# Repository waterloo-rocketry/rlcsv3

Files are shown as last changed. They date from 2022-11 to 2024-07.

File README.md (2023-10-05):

# Remote Launch Control System

RLCS stands for Remote Launch Control System. It's purpose is to fill our rocket with ethanol and nitrous oxide, then ignite the ignition puck inside the rocket, all from a distance of 3000' away at launch control. To do so, it has control over multiple valves at the rocket, a linear actuator to disconnect the fill arm from the rocket, and 2 ignition coils inside the ignition puck.

### Repository Layout

All Arduino firmware code is in `/src`

All electrical schematics and PCB layouts are in `/schematics`

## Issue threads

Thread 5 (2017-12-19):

Finish writing the client code

akmorrison, 2017-12-19:
The client code doesn't currently work. This should be fixed.

Closed 2018-06-08.

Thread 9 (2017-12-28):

Fuses for relay boards in series with battery ground, not with battery v+

akmorrison, 2017-12-28:
The relay boards (and, to follow convention, the power boards) have inline fuses with the battery inputs, but the fuses are on the low side. Because the entire box has a common ground (and most of the battery inputs come from the same few batteries), there are multiple return paths to ground, so overdrawing current will blow multiple fuses, instead of just one (which would be ideal).

This is relatively easy to fix by moving the fuses to inline with the positive side of the battery input, but that would require having new boards made, and would mean scrapping the ones we have, and the expensive-ish hardware that is soldered to them.

This isn't a safety issue, since all batteries are still fused, but it's pretty dumb to have current return paths through multiple parallel fuses. This should be fixed, but it's not a priority to be fixed this term/competition cycle.

Closed 2020-10-31.

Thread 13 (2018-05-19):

NIO: valves on board the rocket are controlled by 4 digital outputs, not 2

amihaila, 2018-05-19:
`nio_init(...)` (and any related internal stuff) needs to be fixed to reflect this.

Closed 2018-06-08.

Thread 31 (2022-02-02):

Incorrect silkscreen labelling on the I2C relay board v3

ZTeper, 2022-02-02:
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

The silkscreen labels on the daisy chain connectors are incorrect!
Also, the pin order on the two connectors are inconsistent, which makes the rlcs wiring quite unpleasant, due to the 180-degree twist required between boards. The two connectors should have the same orientation, i.e. 12V , 5V in front, SDA, SCL in back.

Closed 2022-11-04.

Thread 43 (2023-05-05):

CAN Support Board Issues

BluCodeGH, 2023-05-05:
- Hole pattern is not correct, the board is currently too wide
- Relay should be powered from the 5-pin connector's +12V, not the actuator +12V

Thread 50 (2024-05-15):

Clientside board issue

JasonBrave, 2024-05-15:
1. Mounting holes cannot fit M3 screws
2. One of the mounting hole get in the way of arduino usb type b cable
3. One of the switch have arduino pin conflict with usb uart
4. for the board to function currently, pullup resistor on the arduino have to be desoldered

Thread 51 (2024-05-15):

Towerside power board issue

JasonBrave, 2024-05-15:
UART for ethernet adapter is on UART0, which is conflict to the USB UART onboard arduino

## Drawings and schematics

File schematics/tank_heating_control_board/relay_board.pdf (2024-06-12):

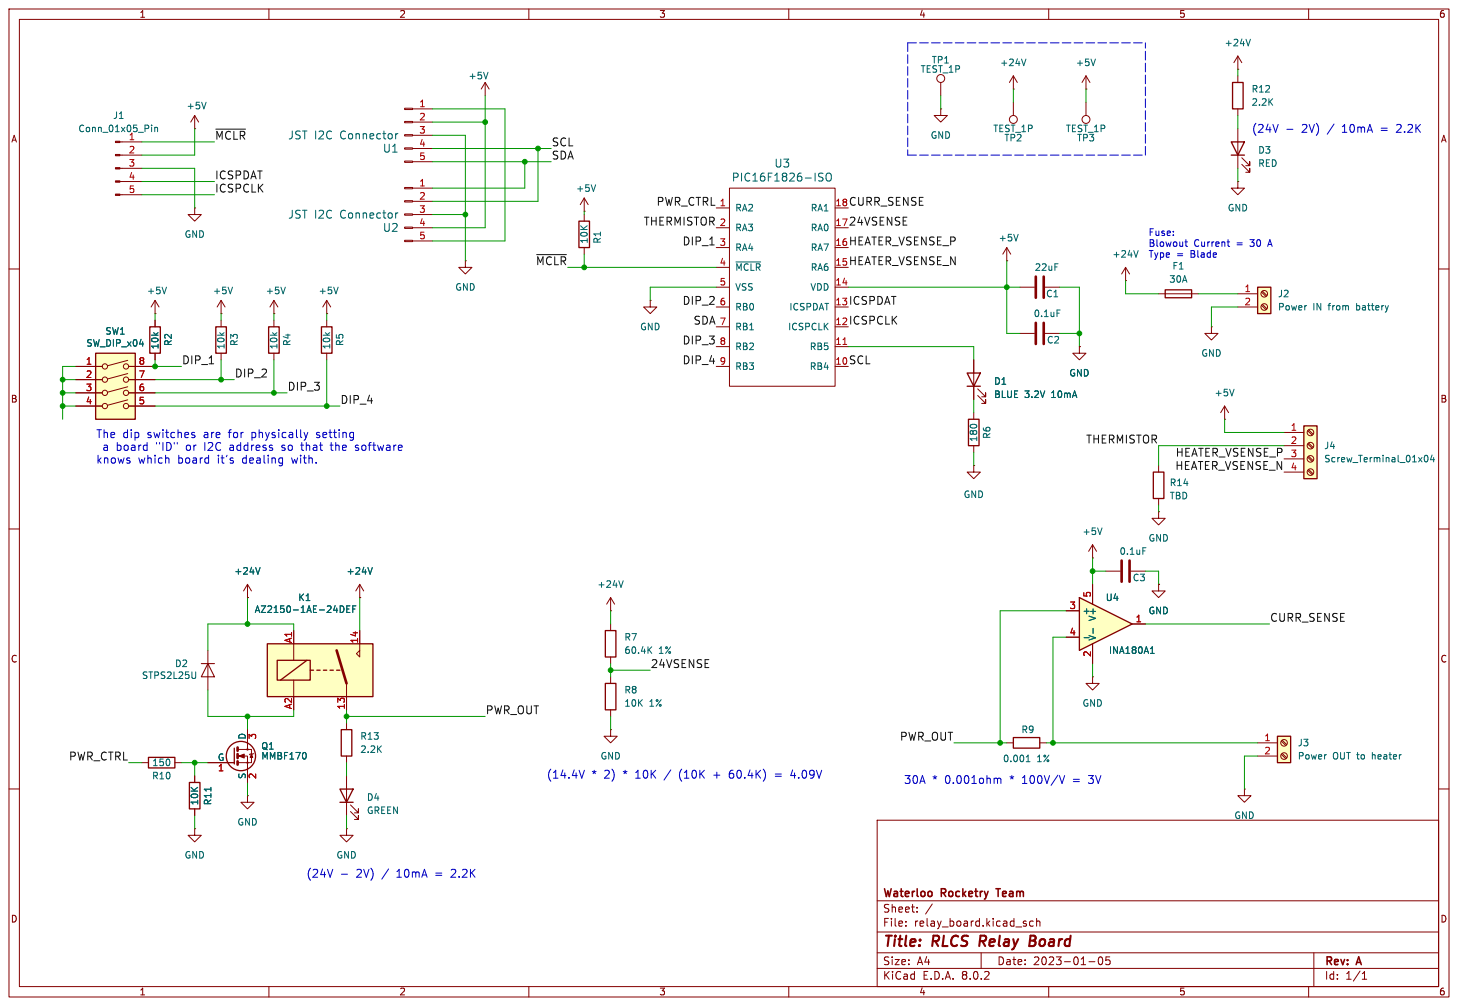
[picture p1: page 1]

a board "ID" or I2C address so that the software

Id: 1/1 Title: RLCS Relay Board

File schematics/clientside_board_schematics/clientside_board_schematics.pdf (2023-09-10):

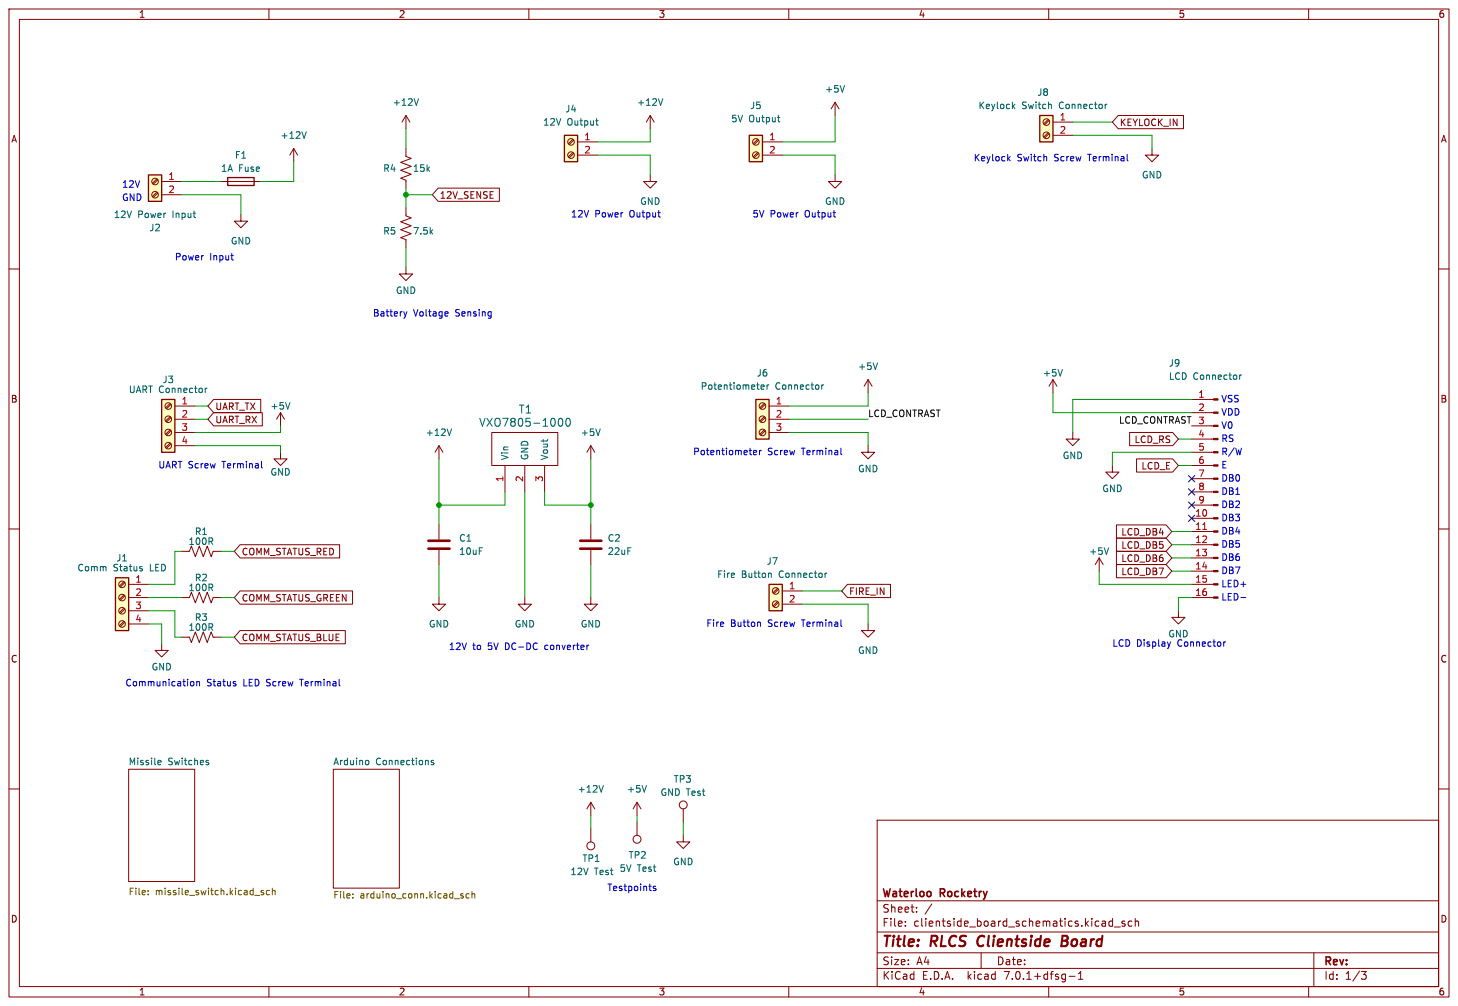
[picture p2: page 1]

Id: 1/3 Title: RLCS Clientside Board

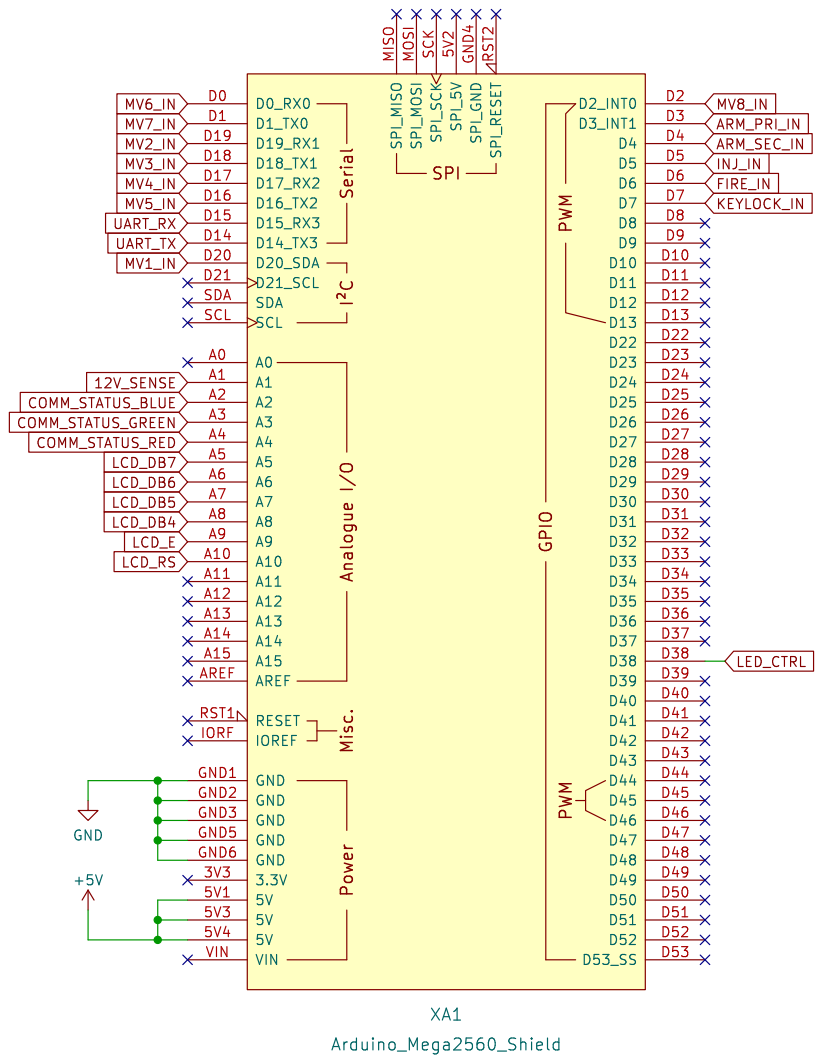
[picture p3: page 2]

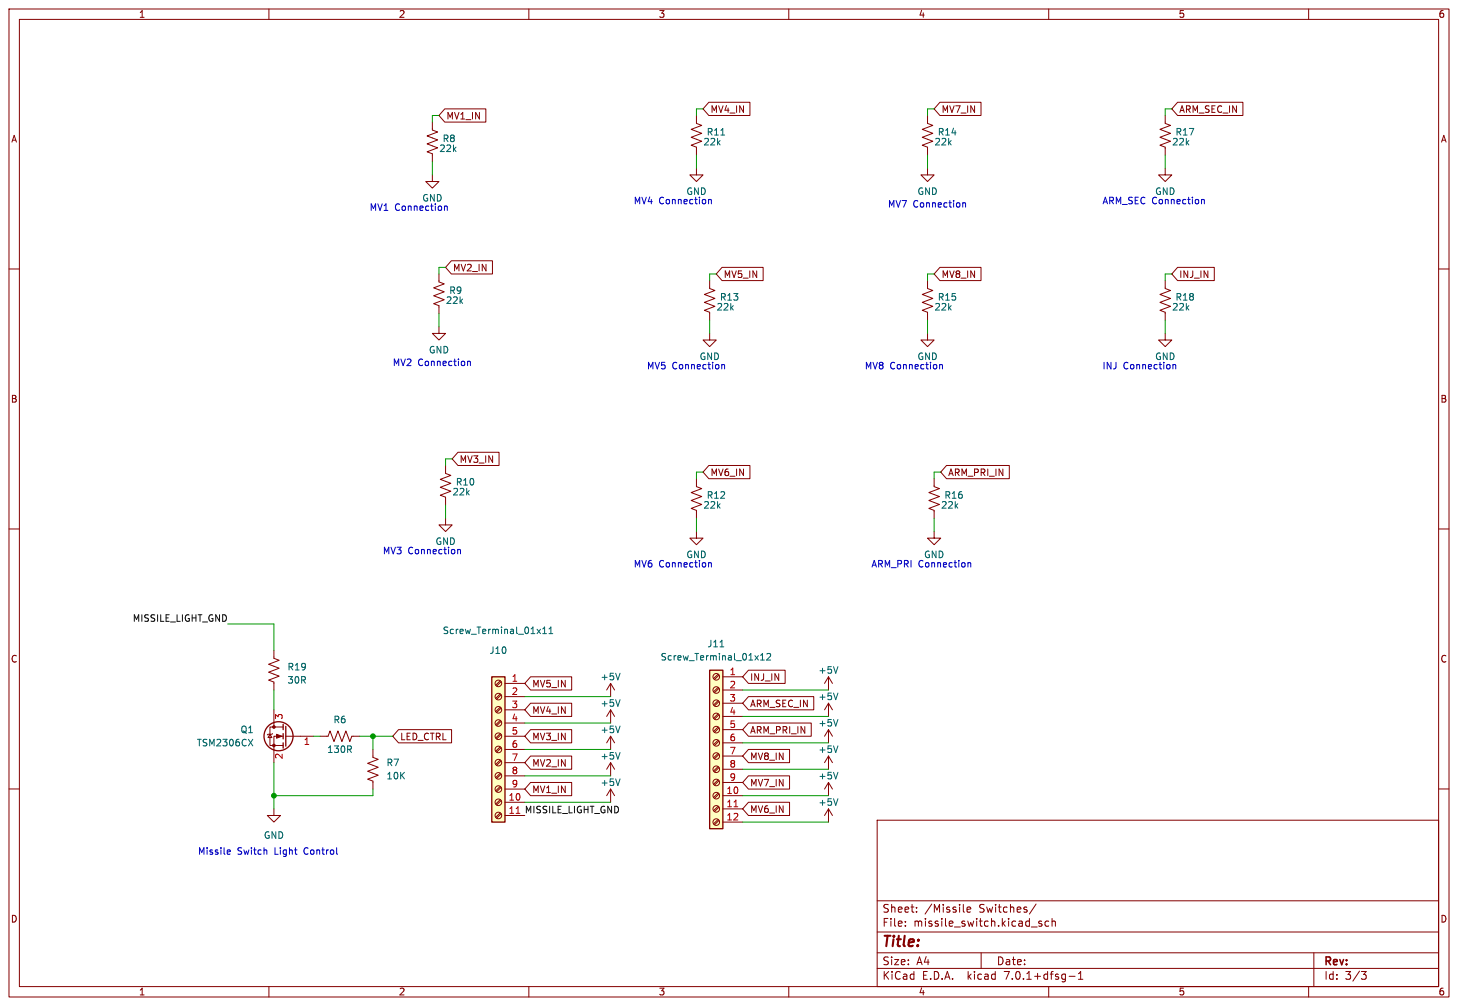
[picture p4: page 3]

INJ Connection MV4 Connection Missile Switch Light Control

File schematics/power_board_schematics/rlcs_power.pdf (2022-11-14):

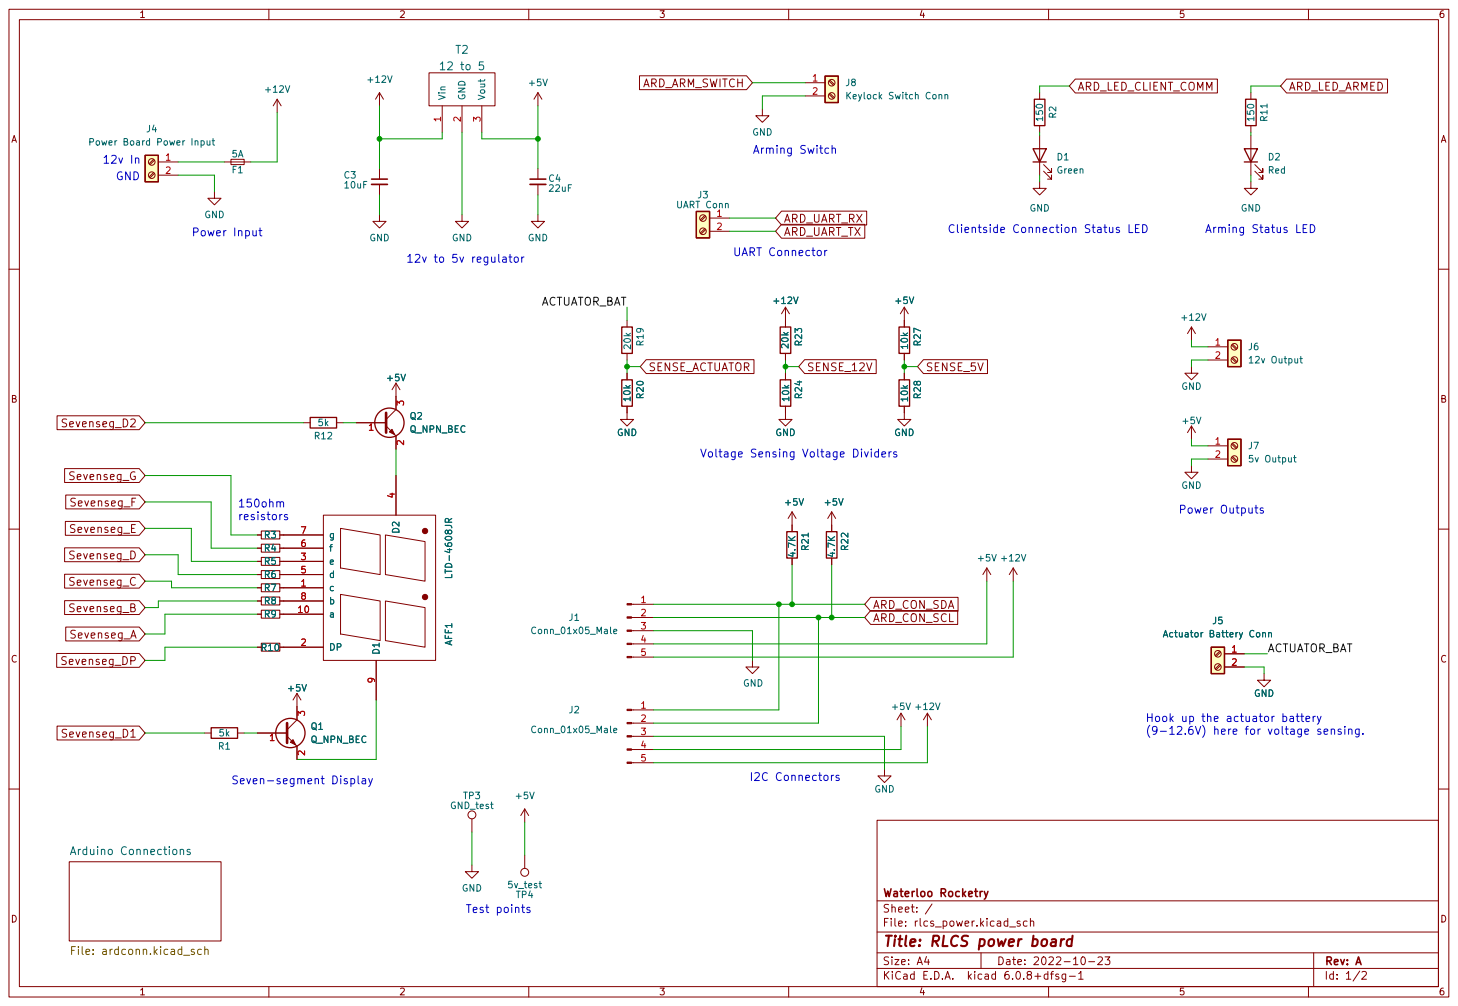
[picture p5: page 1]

Voltage Sensing Voltage Dividers
J1 Conn_01x05_Male TP4

Hook up the actuator battery
(9-12.6V) here for voltage sensing.

File: rlcs_power.kicad_sch Sheet: / Waterloo Rocketry

Id: 1/2 Title: RLCS power board

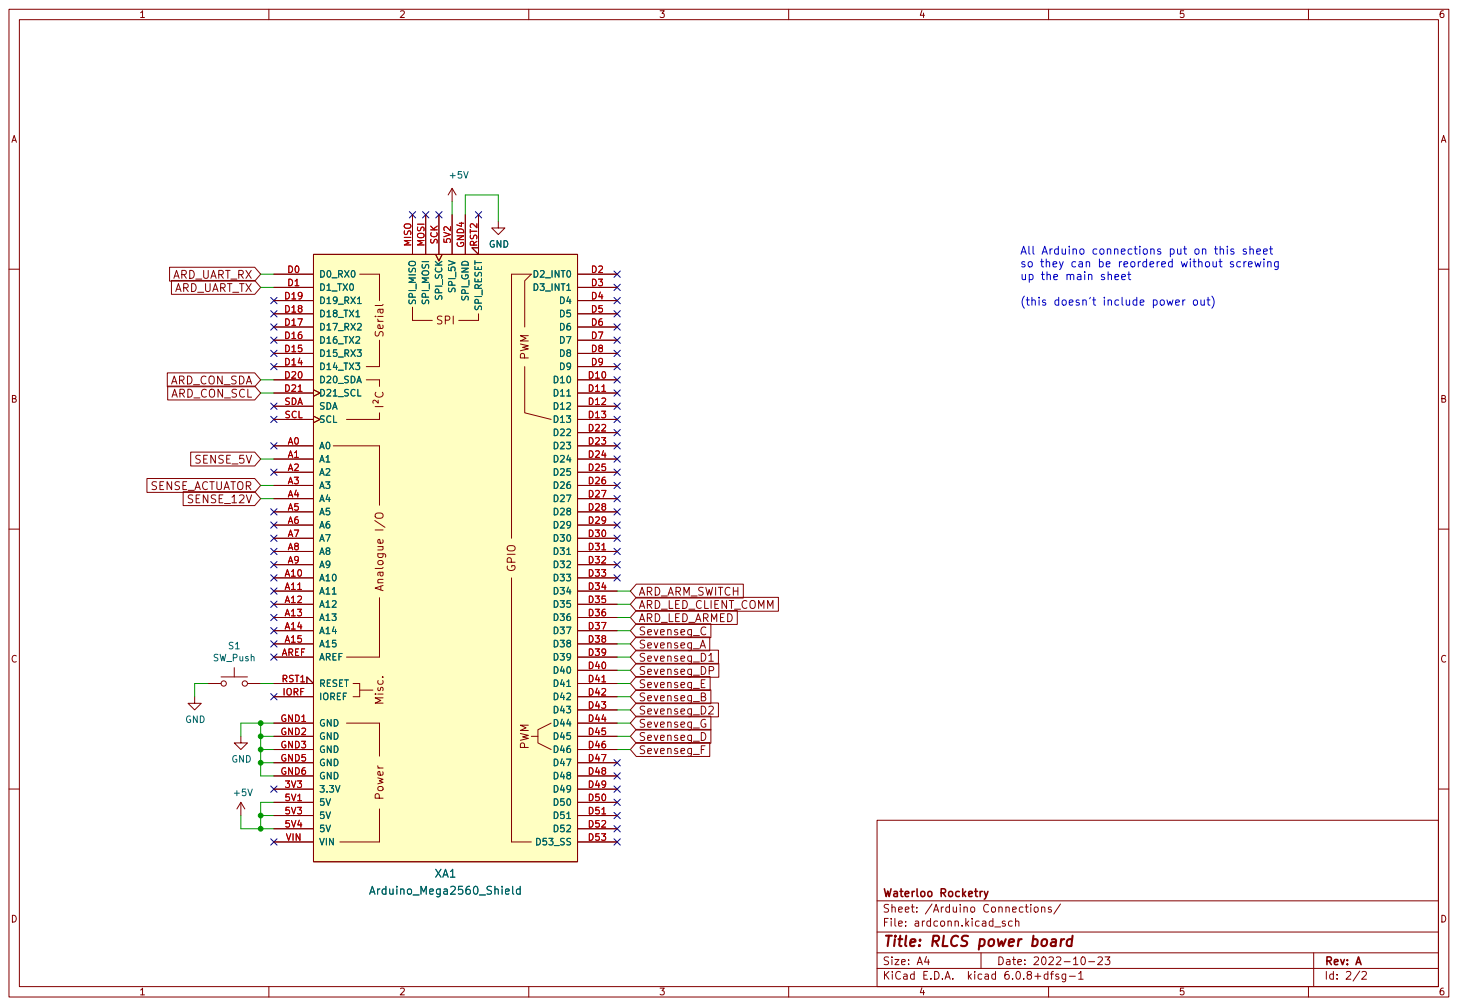
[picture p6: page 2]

All Arduino connections put on this sheet
so they can be reordered without screwing
up the main sheet

(this doesn't include power out) XA1 Arduino_Mega2560_Shield

File: ardconn.kicad_sch Sheet: /Arduino Connections/ Waterloo Rocketry

Id: 2/2 Title: RLCS power board

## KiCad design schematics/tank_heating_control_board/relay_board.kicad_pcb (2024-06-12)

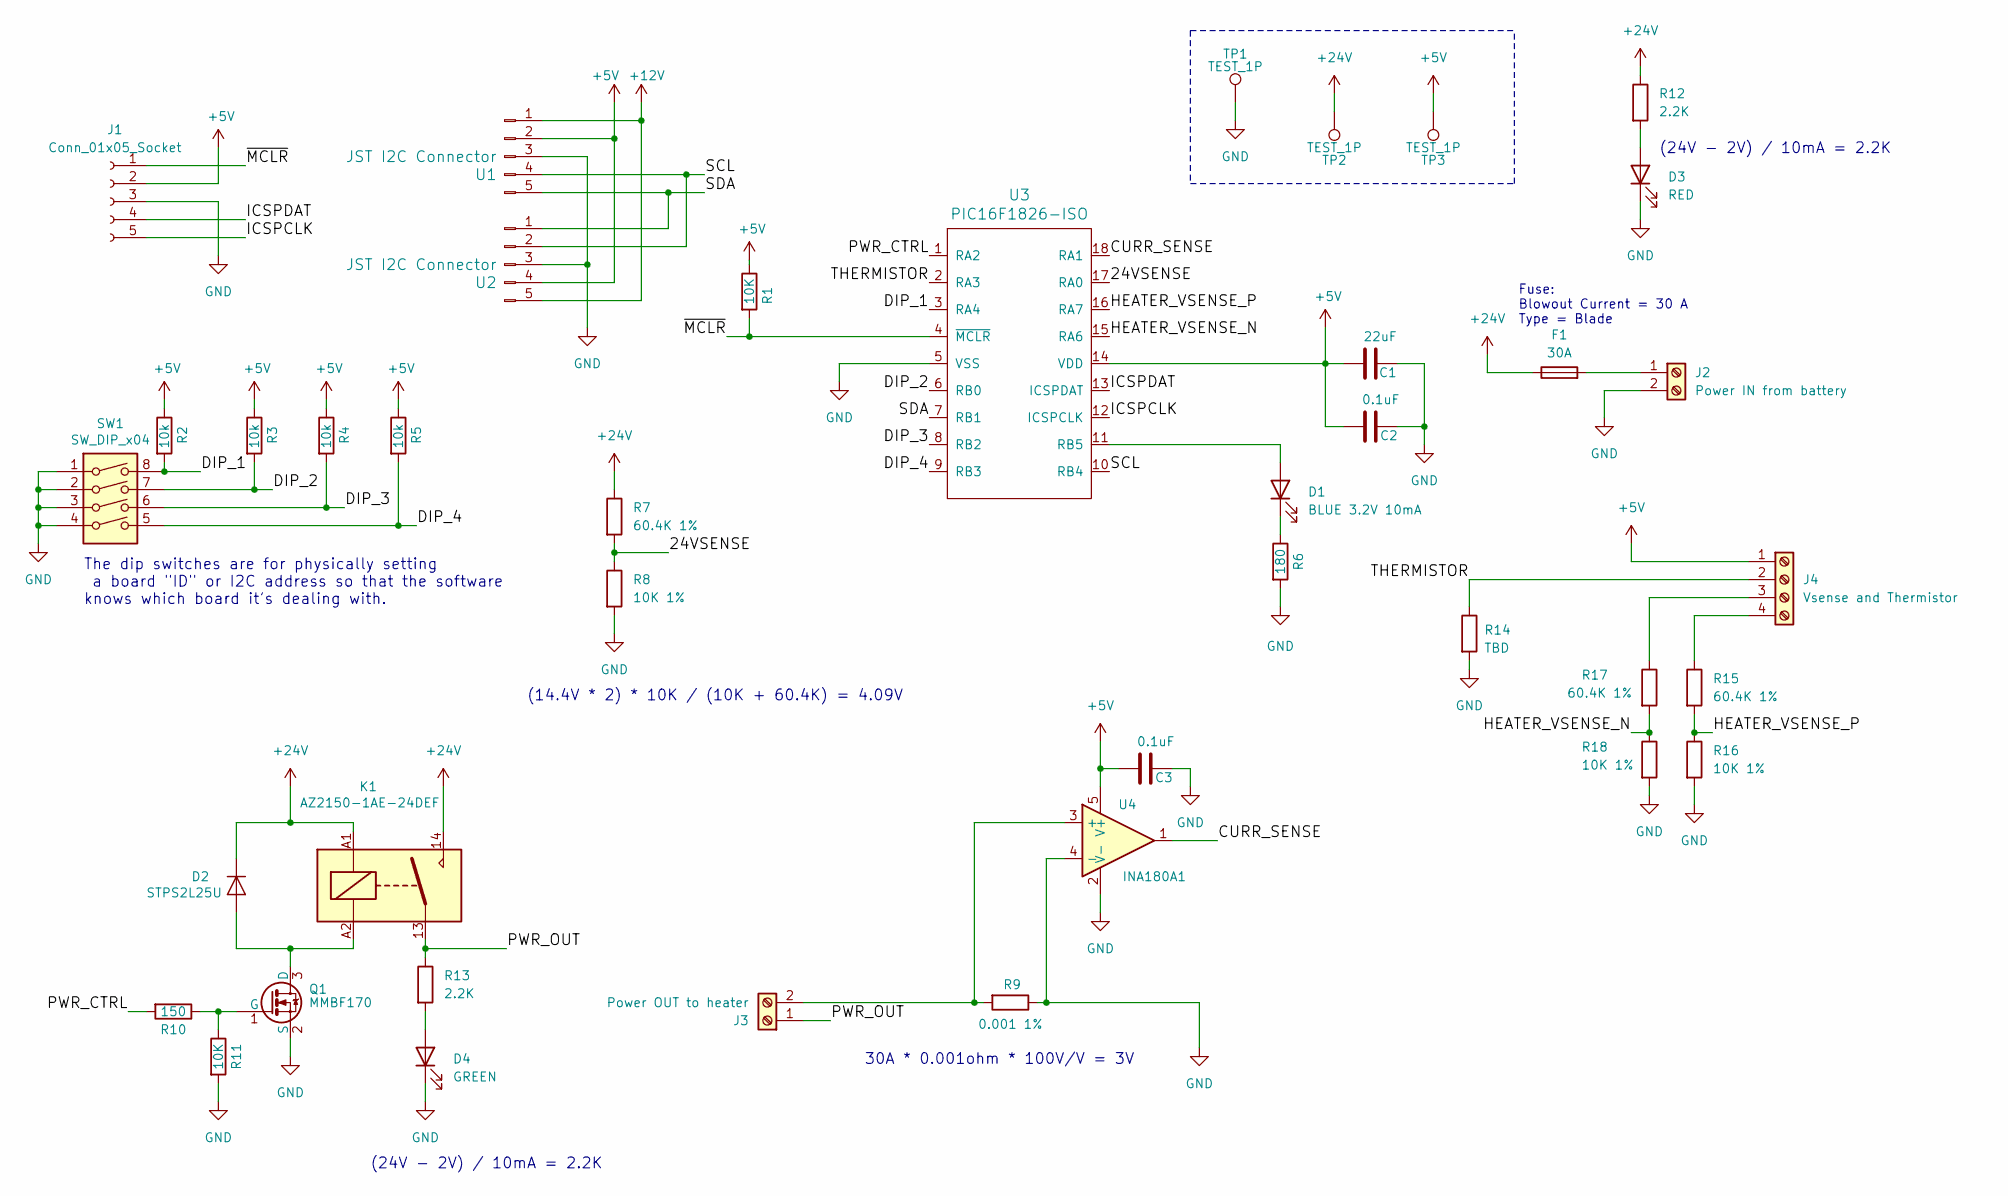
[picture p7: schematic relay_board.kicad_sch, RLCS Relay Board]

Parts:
C1: 22uF; C_0805_2012Metric_Pad1.18x1.45mm_HandSolder
C2, C3: 0.1uF; C_0805_2012Metric_Pad1.18x1.45mm_HandSolder
D1: BLUE 3.2V 10mA; LED_1206_3216Metric_Pad1.42x1.75mm_HandSolder
D2: STPS2L25U; D_SMB_Handsoldering
D3: RED; LED_1206_3216Metric_Pad1.42x1.75mm_HandSolder
D4: GREEN; LED_1206_3216Metric_Pad1.42x1.75mm_HandSolder
F1: 30A; 3557-10_KEY
J1: Conn_01x05_Socket; PinHeader_5x2.54_SMD_90deg_952-3198-1-ND
J2: Power IN from battery; CONN_1714955_PXC
J3: Power OUT to heater; CONN_1714955_PXC
J4: Vsense and Thermistor; TerminalBlock_Phoenix_PT-1,5-4-5.0-H_1x04_P5.00mm_Horizontal
K1: AZ2150-1AE-24DEF; AZ2150_AMZ
Q1: MMBF170; SOT-23
R1, R11: 10K; R_0805_2012Metric_Pad1.20x1.40mm_HandSolder
R2, R3, R4, R5: 10k; R_0805_2012Metric_Pad1.20x1.40mm_HandSolder
R6: 180; R_0805_2012Metric_Pad1.20x1.40mm_HandSolder
R7, R15, R17: 60.4K 1%; R_0805_2012Metric_Pad1.20x1.40mm_HandSolder
R8, R16, R18: 10K 1%; R_0805_2012Metric_Pad1.20x1.40mm_HandSolder
R9: 0.001 1%; R_2512_6332Metric_Pad1.40x3.35mm_HandSolder
R10: 150; R_0805_2012Metric_Pad1.20x1.40mm_HandSolder
R12, R13: 2.2K; R_0805_2012Metric_Pad1.20x1.40mm_HandSolder
R14: TBD; R_0805_2012Metric_Pad1.20x1.40mm_HandSolder
SW1: SW_DIP_x04; DIP_SWITCH_4X2
TP1, TP2, TP3: TEST_1P; Socket_Strip_Straight_1x01_Pitch2.54mm
U1, U2: JST I2C Connector; JST_XH_S5B-XH-A-1_1x05_P2.50mm_Horizontal
U3: PIC16F1826-ISO
U4: INA180A1; SOT-23-5_HandSoldering

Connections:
+5V: C1.1, C2.2, C3.2, J1.2, J4.1, R1.1, R2.1, R3.1, R4.1, R5.1, TP3.1, U1.2, U2.4, U3.14 (VDD), U4.5 (V+)
+12V: U1.1, U2.5
+24V: D2.1 (K), F1.1, K1.14, K1.A1, R7.1, R12.1, TP2.1
/24VSENSE: R7.2, R8.1, U3.17 (RA0)
/CURR_SENSE: U3.18 (RA1), U4.1
/DIP_1: R2.2, SW1.8, U3.3 (RA4)
/DIP_2: R3.2, SW1.7, U3.6 (RB0)
/DIP_3: R4.2, SW1.6, U3.8 (RB2)
/DIP_4: R5.2, SW1.5, U3.9 (RB3)
/HEATER_VSENSE_N: R17.2, R18.1, U3.15 (RA6)
/HEATER_VSENSE_P: R15.2, R16.1, U3.16 (RA7)
/ICSPCLK: J1.5, U3.12 (ICSPCLK)
/ICSPDAT: J1.4, U3.13 (ICSPDAT)
/PWR_CTRL: R10.2, U3.1 (RA2)
/PWR_OUT: J3.1, K1.13, R13.1
/SCL: U1.4, U2.2, U3.10 (RB4)
/SDA: U1.5, U2.1, U3.7 (RB1)
/THERMISTOR: J4.2, R14.1, U3.2 (RA3)
/~MCLR: J1.1, R1.2, U3.4 (~MCLR)
GND: C1.2, C2.1, C3.1, D3.1 (K), D4.1 (K), J1.3, J2.2, Q1.2 (S), R6.2, R8.2, R9.1, R11.2, R14.2, R16.2, R18.2, SW1.1, SW1.2, SW1.3, SW1.4, TP1.1, U1.3, U2.3, U3.5 (VSS), U4.2 (V-), U4.4 (-)
unnamed: D1.2 (A), U3.11 (RB5)
unnamed: D1.1 (K), R6.1
unnamed: D2.2 (A), K1.A2, Q1.3 (D)
unnamed: D3.2 (A), R12.2
unnamed: D4.2 (A), R13.2
unnamed: F1.2, J2.1
unnamed: J3.2, R9.2, U4.3 (+)
unnamed: J4.3, R17.1
unnamed: J4.4, R15.1
unnamed: Q1.1 (G), R10.1, R11.1

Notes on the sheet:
(14.4V * 2) * 10K / (10K + 60.4K) = 4.09V
(24V - 2V) / 10mA = 2.2K
Fuse: Blowout Current = 30 A Type = Blade
30A * 0.001ohm * 100V/V = 3V
The dip switches are for physically setting a board "ID" or I2C address so that the software knows which board it's dealing with.

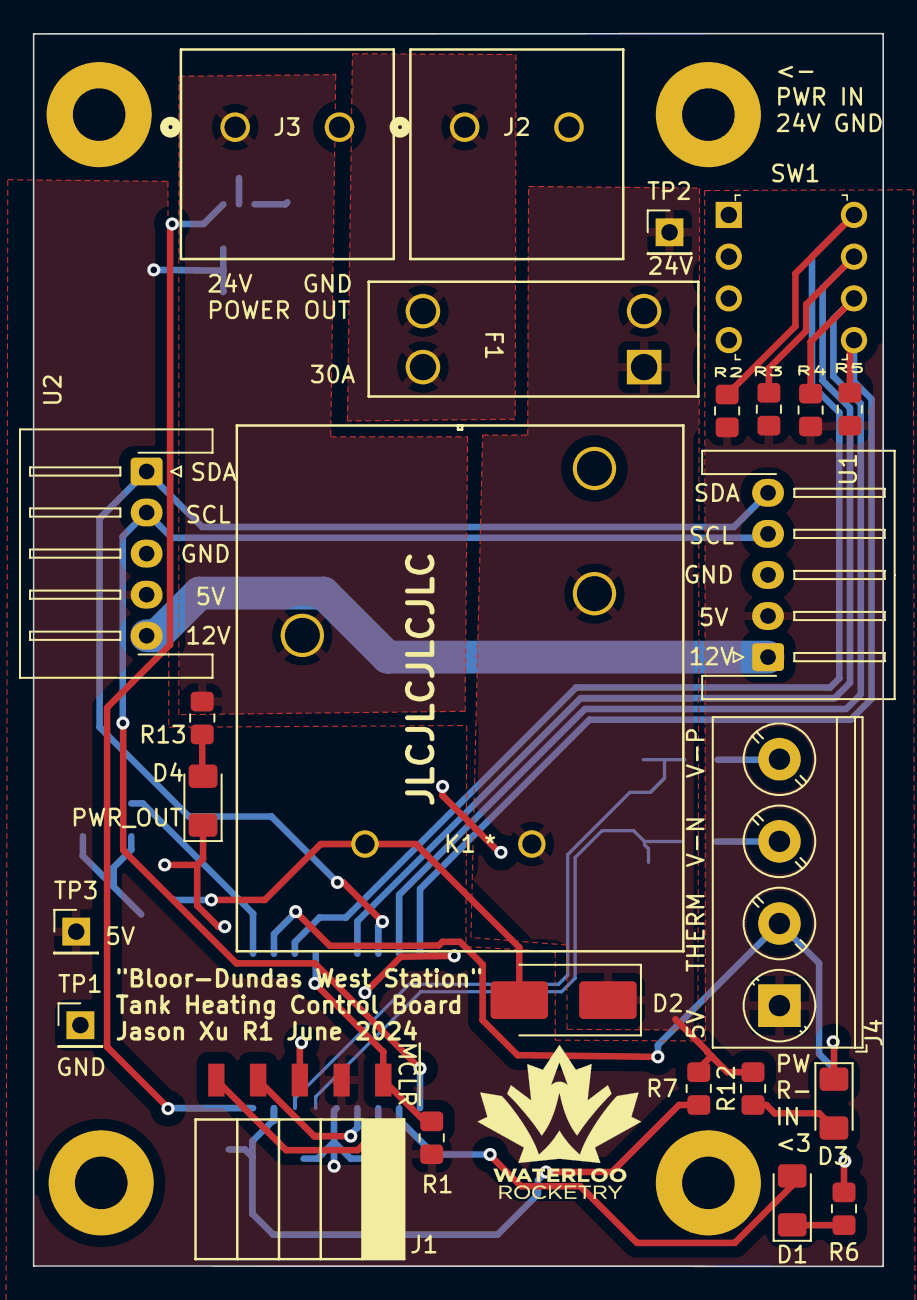
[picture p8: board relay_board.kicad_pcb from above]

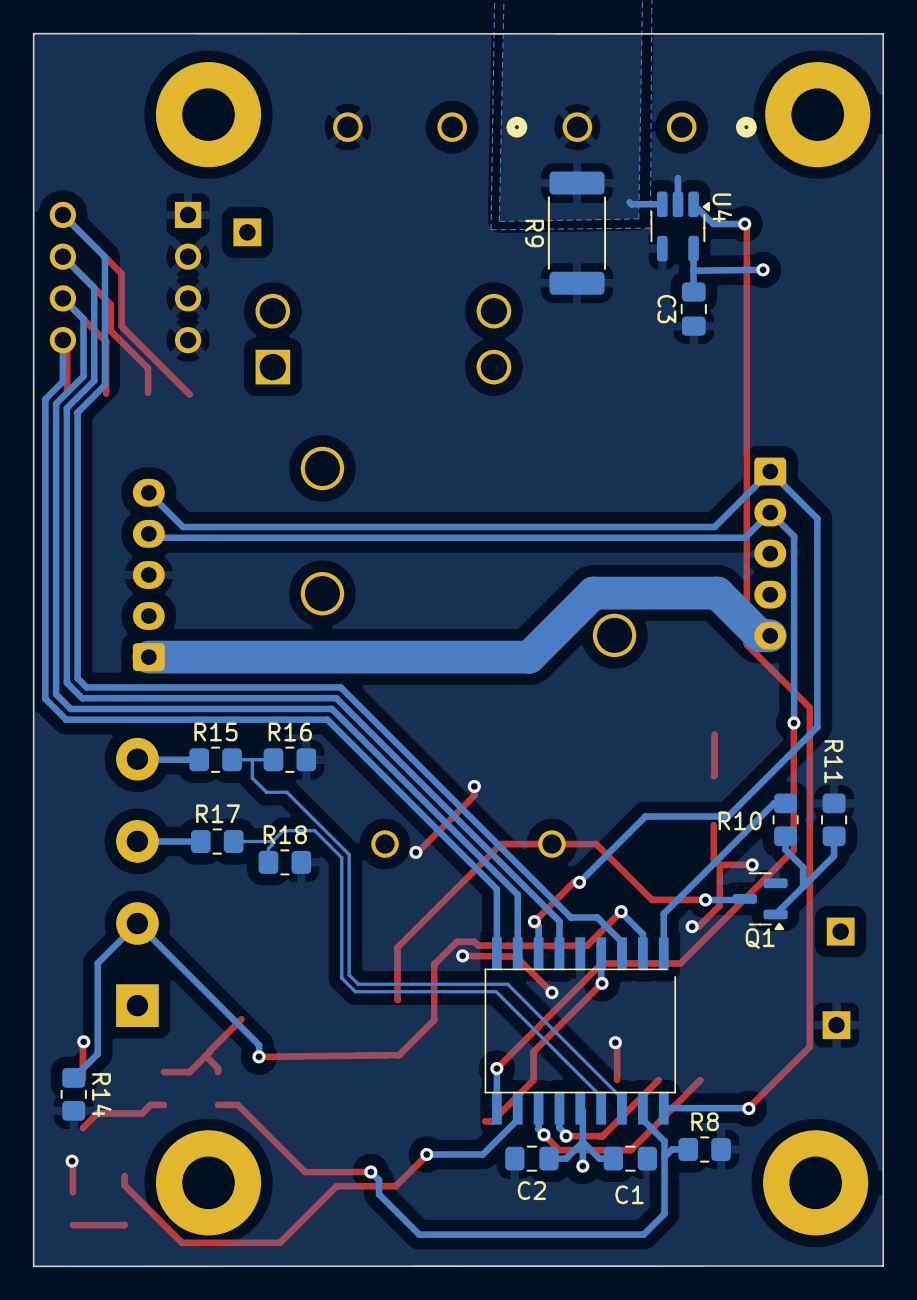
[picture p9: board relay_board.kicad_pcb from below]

Board: 2 copper layers, 51.7 x 75.0 mm, 40 parts (15 on the bottom side), 30 nets.

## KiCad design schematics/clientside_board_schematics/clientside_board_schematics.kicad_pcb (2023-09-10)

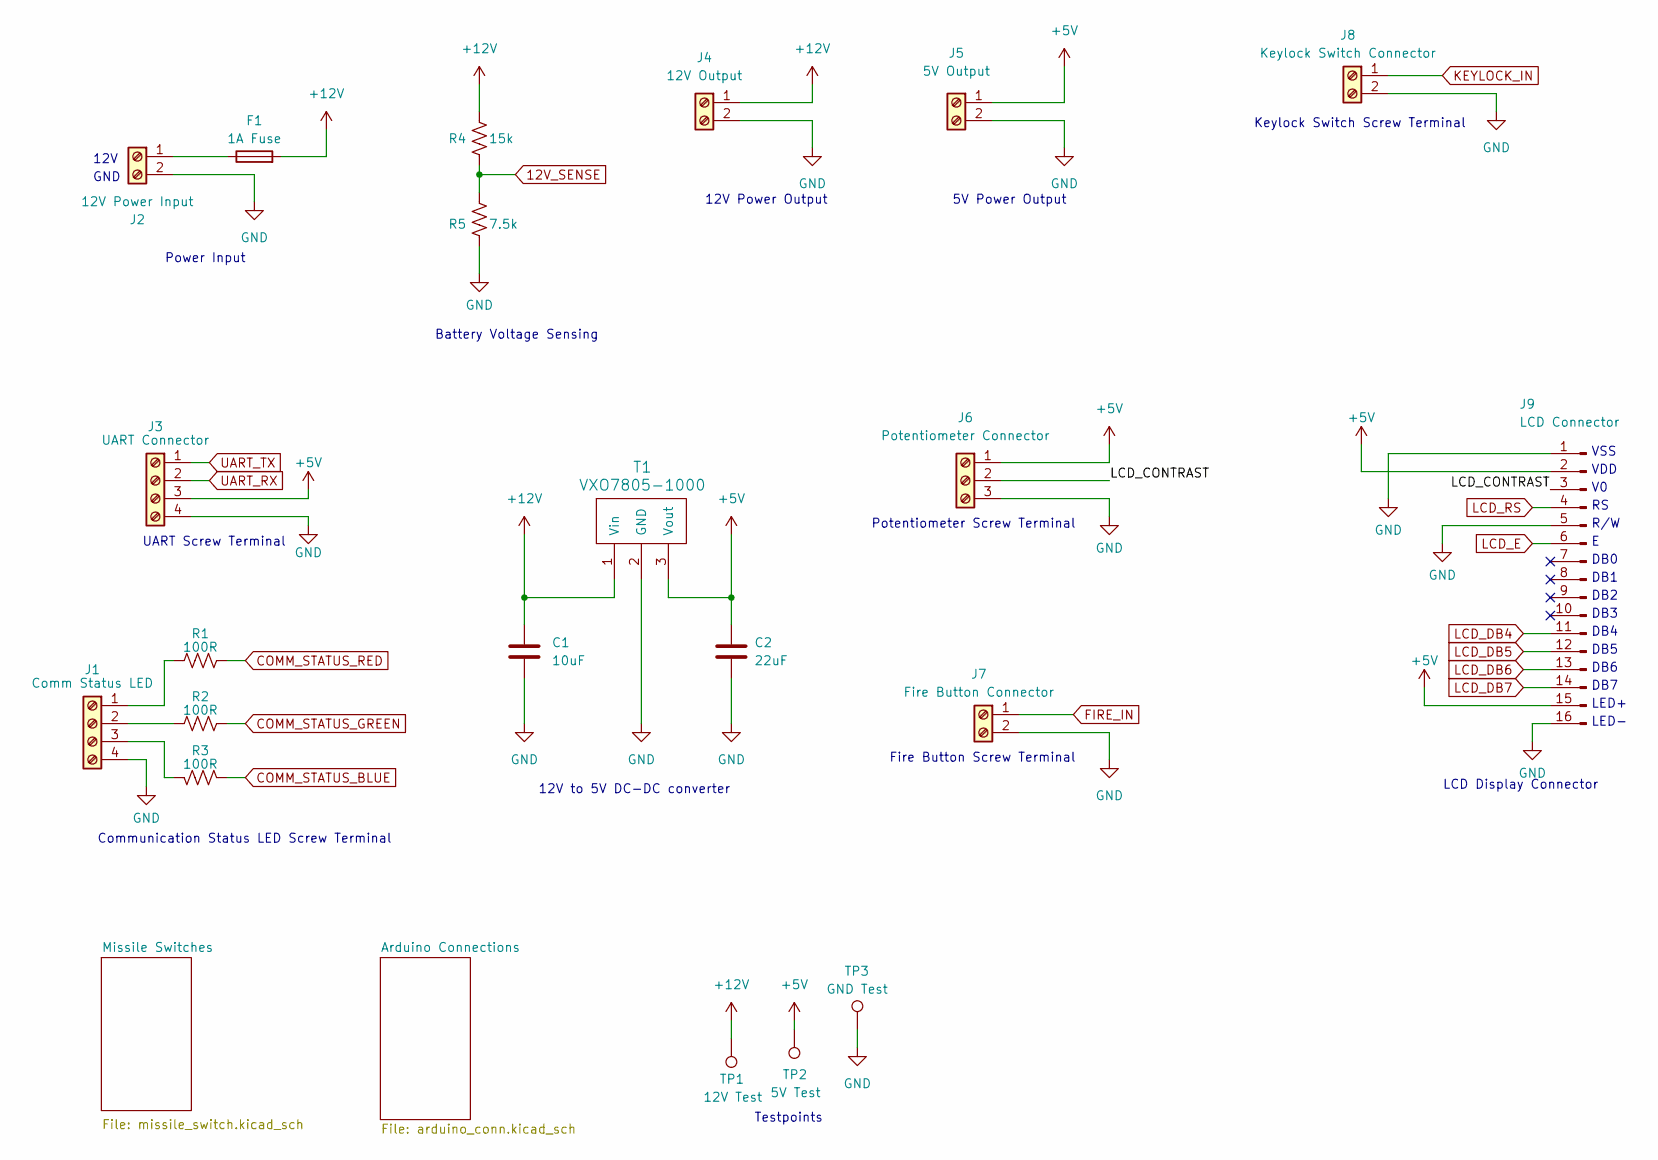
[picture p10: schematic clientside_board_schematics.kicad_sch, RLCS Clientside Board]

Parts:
C1: 10uF; C_0805_2012Metric_Pad1.18x1.45mm_HandSolder
C2: 22uF; C_0805_2012Metric_Pad1.18x1.45mm_HandSolder
F1: 1A Fuse; Fuseholder_Clip-5x20mm_Littelfuse_111_Inline_P20.00x5.00mm_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
J1: Comm Status LED; TerminalBlock_Phoenix_MKDS-1,5-4-5.08_1x04_P5.08mm_Horizont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
J2: 12V Power Input; TerminalBlock_Phoenix_MKDS-1,5-2-5.08_1x02_P5.08mm_Horizont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
J3: UART Connector; TerminalBlock_Phoenix_MKDS-1,5-4-5.08_1x04_P5.08mm_Horizont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
J4: 12V Output; TerminalBlock_Phoenix_MKDS-1,5-2-5.08_1x02_P5.08mm_Horizont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
J5: 5V Output; TerminalBlock_Phoenix_MKDS-1,5-2-5.08_1x02_P5.08mm_Horizont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
J6: Potentiometer Connector; TerminalBlock_Phoenix_MKDS-1,5-3-5.08_1x03_P5.08mm_Horizont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
J7: Fire Button Connector; TerminalBlock_Phoenix_MKDS-1,5-2-5.08_1x02_P5.08mm_Horizont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
J8: Keylock Switch Connector; TerminalBlock_Phoenix_MKDS-1,5-2-5.08_1x02_P5.08mm_Horizont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
J9: LCD Connector; NHD-0420DZ-FSW-FBW
R1, R2, R3: 100R; R_0805_2012Metric_Pad1.20x1.40mm_HandSolder
R4: 15k; R_0805_2012Metric_Pad1.20x1.40mm_HandSolder
R5: 7.5k; R_0805_2012Metric_Pad1.20x1.40mm_HandSolder
T1: VXO7805-1000; VXO78XX-1000
TP1: 12V Test; PinSocket_1x01_P2.00mm_Vertical
TP2: 5V Test; PinSocket_1x01_P2.00mm_Vertical
TP3: GND Test; PinSocket_1x01_P2.00mm_Vertical

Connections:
12V_SENSE: R4.2, R5.1; also elsewhere on the board
+5V: C2.1, J3.3, J5.1, J6.1, J9.2, J9.15, T1.3 (Vout), TP2.1; also elsewhere on the board
+12V: C1.1, F1.2, J4.1, R4.1, T1.1 (Vin), TP1.1
/LCD_CONTRAST: J6.2, J9.3
COMM_STATUS_BLUE: R3.2; also elsewhere on the board
COMM_STATUS_GREEN: R2.2; also elsewhere on the board
COMM_STATUS_RED: R1.2; also elsewhere on the board
FIRE_IN: J7.1; also elsewhere on the board
GND: C1.2, C2.2, J1.4, J2.2, J3.4, J4.2, J5.2, J6.3, J7.2, J8.2, J9.1, J9.5, J9.16, R5.2, T1.2 (GND), TP3.1; also elsewhere on the board
KEYLOCK_IN: J8.1; also elsewhere on the board
LCD_DB4: J9.11; also elsewhere on the board
LCD_DB5: J9.12; also elsewhere on the board
LCD_DB6: J9.13; also elsewhere on the board
LCD_DB7: J9.14; also elsewhere on the board
LCD_E: J9.6; also elsewhere on the board
LCD_RS: J9.4; also elsewhere on the board
unnamed: J1.1, R1.1
unnamed: J1.2, R2.1
unnamed: J1.3, R3.1
unnamed: F1.1, J2.1
UART_RX: J3.2; also elsewhere on the board
UART_TX: J3.1; also elsewhere on the board

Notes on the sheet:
LED-
Battery Voltage Sensing
DB0
R/W
DB2
5V Power Output
Keylock Switch Screw Terminal
DB6
GND
12V
LED+
12V Power Output
DB4
DB7
VSS
VDD
Potentiometer Screw Terminal
Testpoints
LCD Display Connector
DB3
Fire Button Screw Terminal
DB5
Power Input
DB1
UART Screw Terminal
12V to 5V DC-DC converter
Communication Status LED Screw Terminal

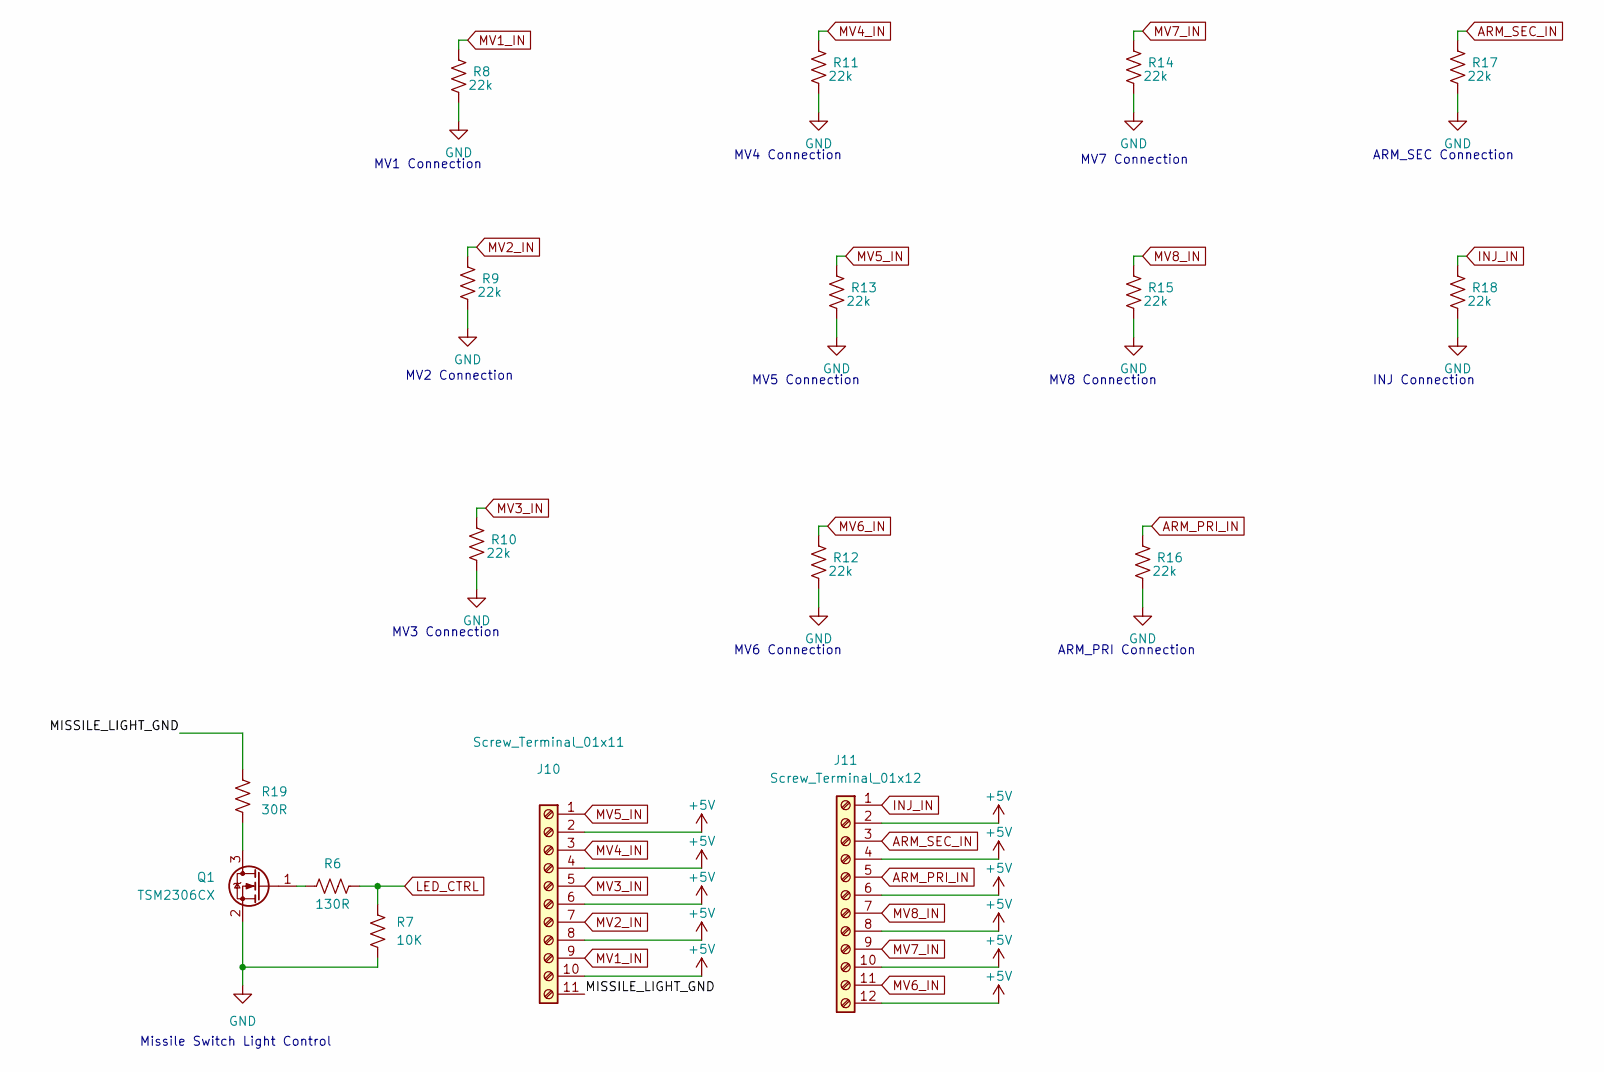
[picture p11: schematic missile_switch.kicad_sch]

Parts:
J10: Screw_Terminal_01x11; TerminalBlock_Phoenix_PT-1,5-11-3.5-H_1x11_P3.50mm_Horizont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
J11: Screw_Terminal_01x12; TerminalBlock_Phoenix_PT-1,5-12-3.5-H_1x12_P3.50mm_Horizont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
Q1: TSM2306CX; SOT-23_Handsoldering
R6: 130R; R_0805_2012Metric_Pad1.20x1.40mm_HandSolder
R7: 10K; R_0805_2012Metric_Pad1.20x1.40mm_HandSolder
R8, R9, R10, R11, R12, R13, R14, R15, R16, R17, R18: 22k; R_0805_2012Metric_Pad1.20x1.40mm_HandSolder
R19: 30R; R_0805_2012Metric_Pad1.20x1.40mm_HandSolder

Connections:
+5V: J10.2, J10.4, J10.6, J10.8, J10.10, J11.2, J11.4, J11.6, J11.8, J11.10, J11.12; also elsewhere on the board
/Missile Switches/MISSILE_LIGHT_GND: J10.11, R19.1
ARM_PRI_IN: J11.5, R16.1; also elsewhere on the board
ARM_SEC_IN: J11.3, R17.1; also elsewhere on the board
GND: Q1.2 (S), R7.2, R8.2, R9.2, R10.2, R11.2, R12.2, R13.2, R14.2, R15.2, R16.2, R17.2, R18.2; also elsewhere on the board
INJ_IN: J11.1, R18.1; also elsewhere on the board
LED_CTRL: R6.2, R7.1; also elsewhere on the board
MV1_IN: J10.9, R8.1; also elsewhere on the board
MV2_IN: J10.7, R9.1; also elsewhere on the board
MV3_IN: J10.5, R10.1; also elsewhere on the board
MV4_IN: J10.3, R11.1; also elsewhere on the board
MV5_IN: J10.1, R13.1; also elsewhere on the board
MV6_IN: J11.11, R12.1; also elsewhere on the board
MV7_IN: J11.9, R14.1; also elsewhere on the board
MV8_IN: J11.7, R15.1; also elsewhere on the board
unnamed: Q1.3 (D), R19.2
unnamed: Q1.1 (G), R6.1

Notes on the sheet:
MV8 Connection
MV3 Connection
ARM_SEC Connection
MV4 Connection
INJ Connection
MV6 Connection
MV1 Connection
MV5 Connection
MV7 Connection
ARM_PRI Connection
Missile Switch Light Control
MV2 Connection

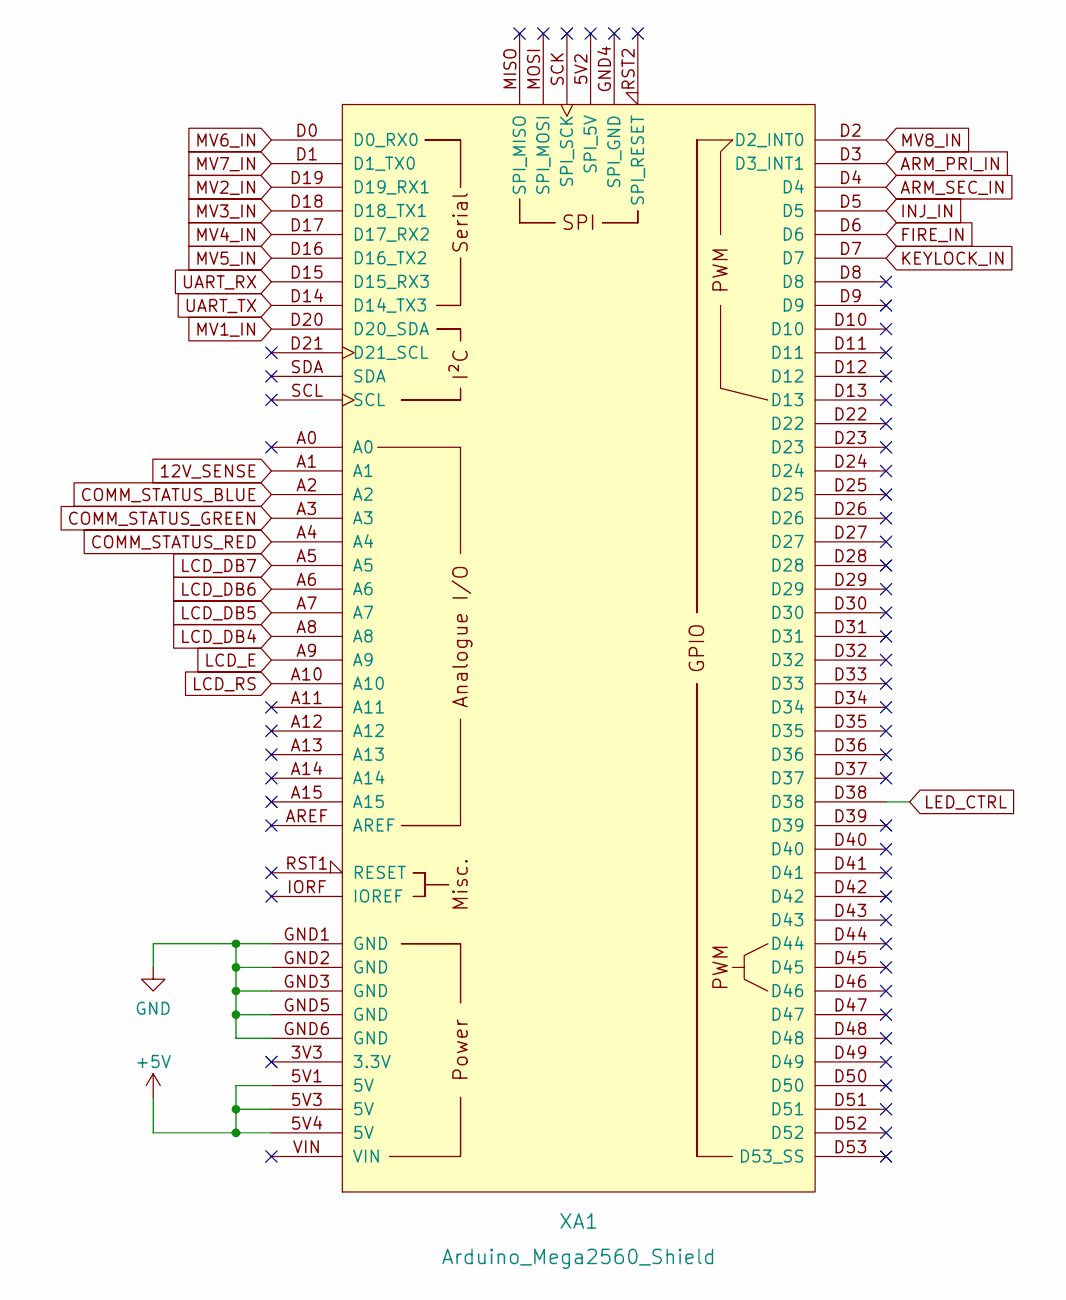
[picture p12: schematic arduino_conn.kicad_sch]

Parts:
XA1: Arduino_Mega2560_Shield

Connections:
12V_SENSE: XA1.A1; also elsewhere on the board
+5V: XA1.5V1 (5V), XA1.5V3 (5V), XA1.5V4 (5V); also elsewhere on the board
ARM_PRI_IN: XA1.D3 (D3_INT1); also elsewhere on the board
ARM_SEC_IN: XA1.D4; also elsewhere on the board
COMM_STATUS_BLUE: XA1.A2; also elsewhere on the board
COMM_STATUS_GREEN: XA1.A3; also elsewhere on the board
COMM_STATUS_RED: XA1.A4; also elsewhere on the board
FIRE_IN: XA1.D6; also elsewhere on the board
GND: XA1.GND1 (GND), XA1.GND2 (GND), XA1.GND3 (GND), XA1.GND5 (GND), XA1.GND6 (GND); also elsewhere on the board
INJ_IN: XA1.D5; also elsewhere on the board
KEYLOCK_IN: XA1.D7; also elsewhere on the board
LCD_DB4: XA1.A8; also elsewhere on the board
LCD_DB5: XA1.A7; also elsewhere on the board
LCD_DB6: XA1.A6; also elsewhere on the board
LCD_DB7: XA1.A5; also elsewhere on the board
LCD_E: XA1.A9; also elsewhere on the board
LCD_RS: XA1.A10; also elsewhere on the board
LED_CTRL: XA1.D38; also elsewhere on the board
MV1_IN: XA1.D20 (D20_SDA); also elsewhere on the board
MV2_IN: XA1.D19 (D19_RX1); also elsewhere on the board
MV3_IN: XA1.D18 (D18_TX1); also elsewhere on the board
MV4_IN: XA1.D17 (D17_RX2); also elsewhere on the board
MV5_IN: XA1.D16 (D16_TX2); also elsewhere on the board
MV6_IN: XA1.D0 (D0_RX0); also elsewhere on the board
MV7_IN: XA1.D1 (D1_TX0); also elsewhere on the board
MV8_IN: XA1.D2 (D2_INT0); also elsewhere on the board
UART_RX: XA1.D15 (D15_RX3); also elsewhere on the board
UART_TX: XA1.D14 (D14_TX3); also elsewhere on the board

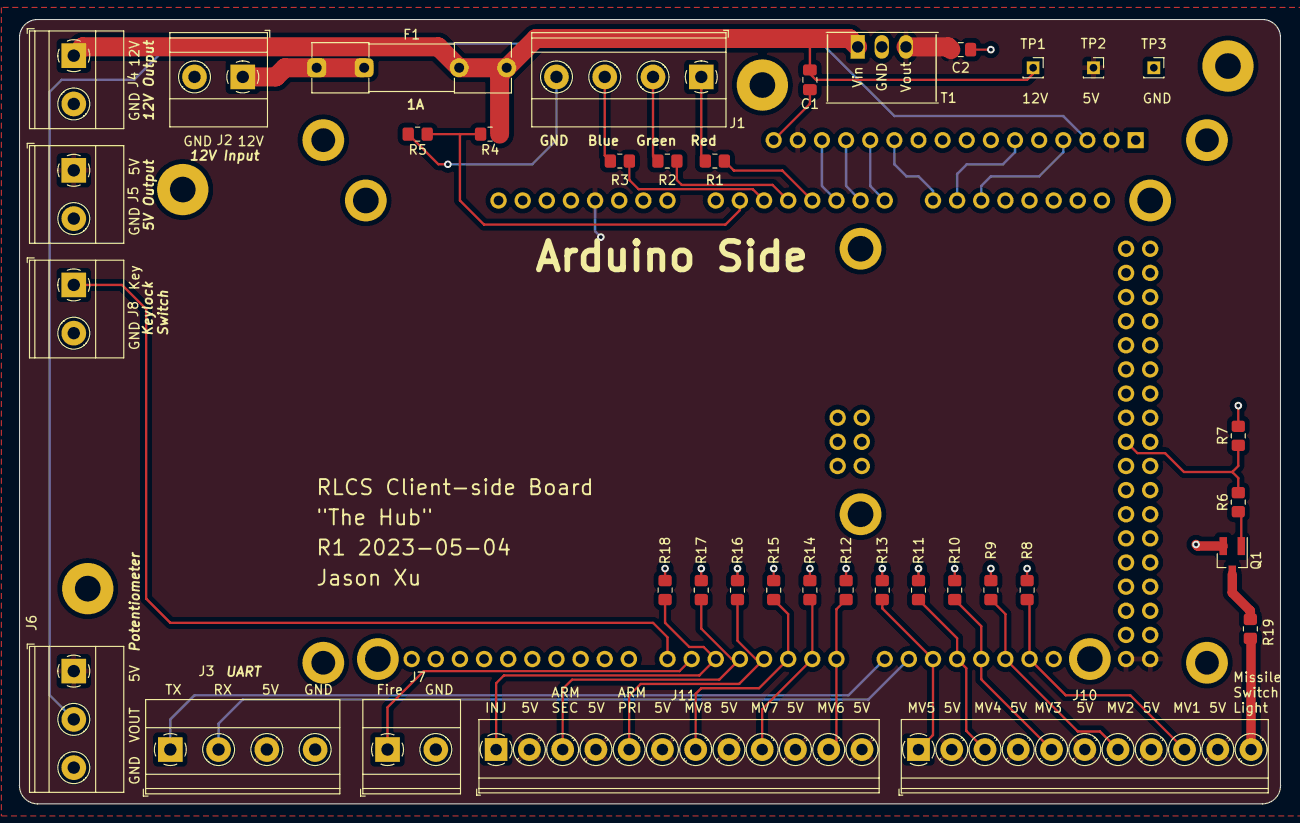
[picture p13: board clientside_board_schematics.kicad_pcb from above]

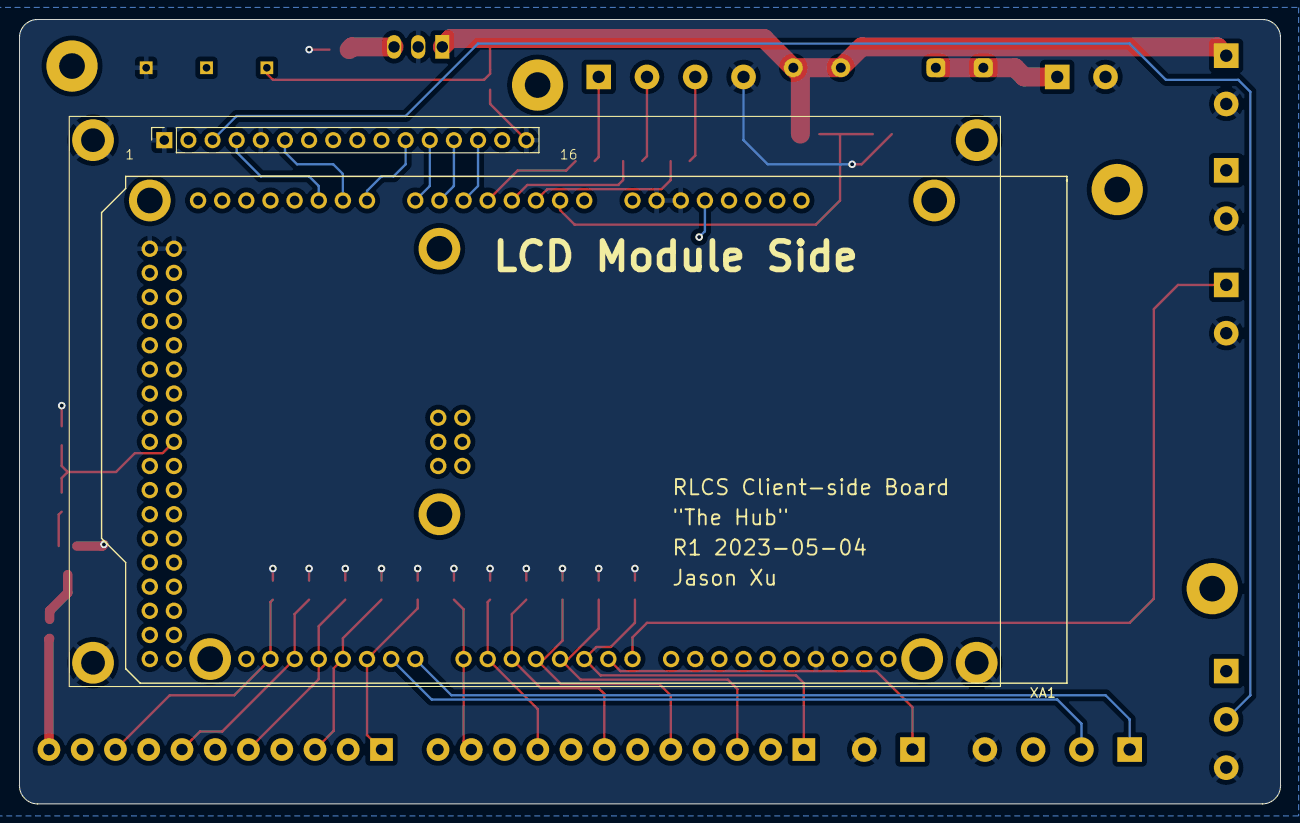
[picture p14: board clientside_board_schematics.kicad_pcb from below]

Board: 2 copper layers, 132.7 x 82.6 mm, 43 parts (2 on the bottom side), 37 nets.

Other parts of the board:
Left Mount: MountingHole_2.7mm_M2.5_Pad
Top Mount: MountingHole_2.7mm_M2.5_Pad
Top-Left Mount: MountingHole_2.7mm_M2.5_Pad
Top-Right Mount: MountingHole_2.7mm_M2.5_Pad

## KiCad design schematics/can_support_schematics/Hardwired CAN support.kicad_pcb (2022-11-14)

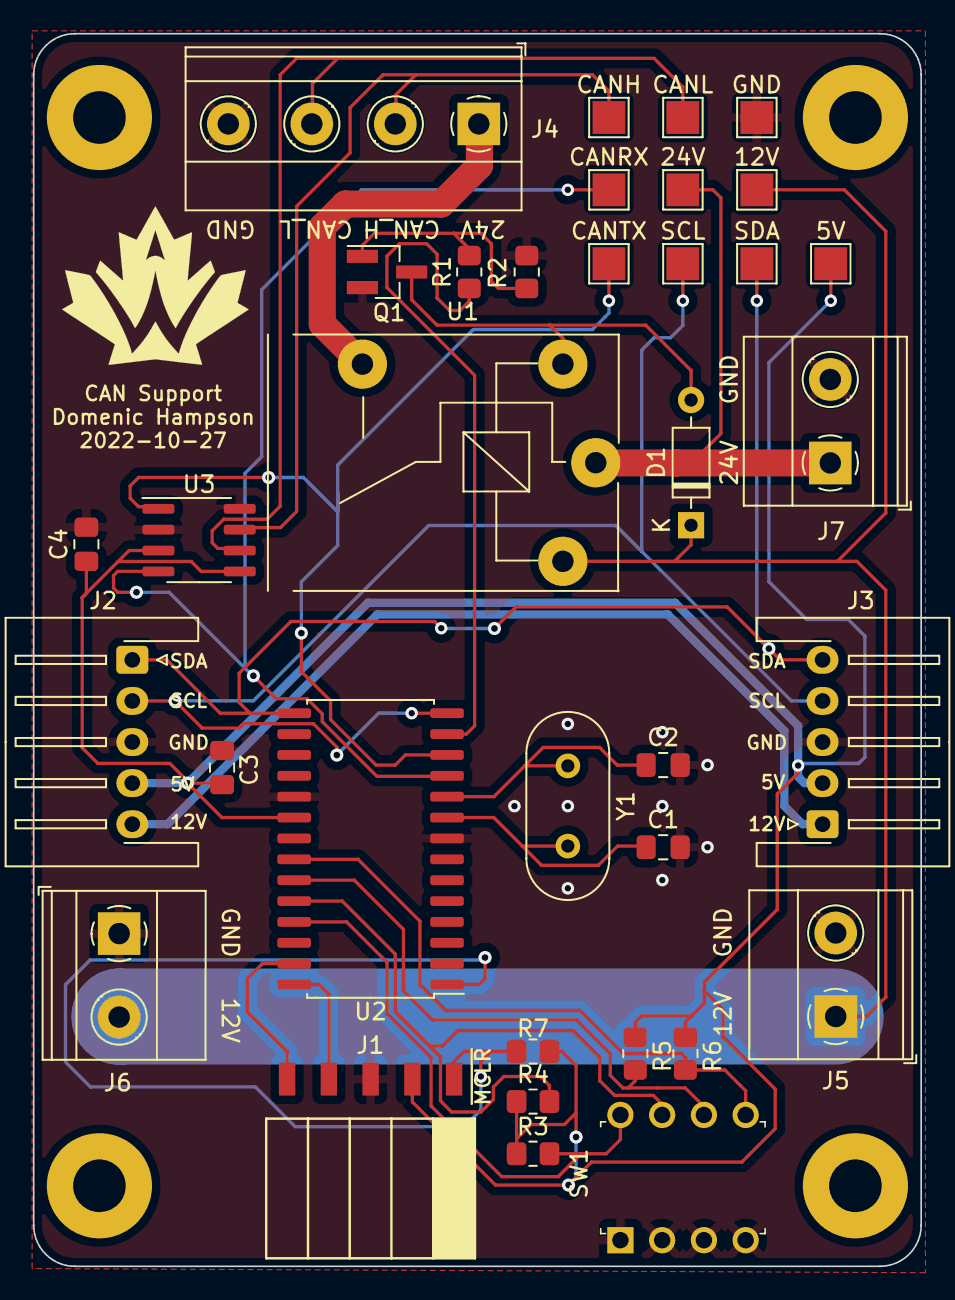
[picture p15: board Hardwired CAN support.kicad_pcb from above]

Board: 2 copper layers, 54.0 x 75.0 mm, 35 parts (0 on the bottom side), 24 nets.

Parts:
5V, 12V, 24V: TestPoint; TestPoint_THTPad_2.0x2.0mm_Drill1.0mm
C1, C2: 27pF; C_0805_2012Metric_Pad1.18x1.45mm_HandSolder
C3: 0.1uF; C_0805_2012Metric_Pad1.18x1.45mm_HandSolder
C4: 10uF; C_0805_2012Metric_Pad1.18x1.45mm_HandSolder
CANH: TestPoint; TestPoint_THTPad_2.0x2.0mm_Drill1.0mm
CANL: TestPoint; TestPoint_THTPad_2.0x2.0mm_Drill1.0mm
CANRX: TestPoint; TestPoint_THTPad_2.0x2.0mm_Drill1.0mm
CANTX: TestPoint; TestPoint_THTPad_2.0x2.0mm_Drill1.0mm
D1: D; D_DO-35_SOD27_P7.62mm_Horizontal
GND: TestPoint; TestPoint_THTPad_2.0x2.0mm_Drill1.0mm
J1: Conn_01x05_Female; PinHeader_5x2.54_SMD_90deg_952-3198-1-ND
J2, J3: Conn_01x05_Male; JST_XH_S5B-XH-A-1_1x05_P2.50mm_Horizontal
J4: Screw_Terminal_01x04; TerminalBlock_Phoenix_MKDS-1,5-4-5.08_1x04_P5.08mm_Horizont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
J5, J6, J7: Screw_Terminal_01x02; TerminalBlock_Phoenix_MKDS-1,5-2-5.08_1x02_P5.08mm_Horizont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
Q1: MMBF170; SOT-23_Handsoldering
R1: 150R; R_0805_2012Metric_Pad1.20x1.40mm_HandSolder
R2: 10K; R_0805_2012Metric_Pad1.20x1.40mm_HandSolder
R3, R4, R5, R6, R7: 10k; R_0805_2012Metric_Pad1.20x1.40mm_HandSolder
SCL: TestPoint; TestPoint_THTPad_2.0x2.0mm_Drill1.0mm
SDA: TestPoint; TestPoint_THTPad_2.0x2.0mm_Drill1.0mm
SW1: SW_DIP_x04; DIP_SWITCH_4X2
U1: SPST_POWER_RELAY; Relay_SPST_G5LE-1A
U2: PIC18F26K83; SOIC-28W_7.5x17.9mm_P1.27mm
U3: MCP2562; SOIC-8_3.9x4.9mm_P1.27mm
Y1: Crystal; Crystal_HC49-4H_Vertical

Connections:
+5V: 5V.1, C3.1, C4.1, J1.2, J2.4, J3.2, R3.1, R4.1, R5.1, R6.1, R7.1, U2.20 (VDD), U3.3 (VDD), U3.5 (VIO)
+12V: 12V.1, D1.1 (K), J5.1, J6.2, U1.1 (CIN)
+24V: 24V.1, J7.1, U1.3 (SIN)
/BASE: Q1.1 (G), R1.2, R2.1
/CAN_H: CANH.1, J4.2, U3.7 (CANH)
/CAN_L: CANL.1, J4.3, U3.6 (CANL)
/CAN_RX: CANRX.1, U2.11 (RC0), U3.4 (RXD)
/CAN_TX: CANTX.1, U2.12 (RC1), U3.1 (TXD)
/DIP_1: R3.2, SW1.8, U2.25 (RB4)
/DIP_2: R4.2, SW1.7, U2.24 (RB3)
/DIP_3: R5.2, SW1.6, U2.23 (RB2)
/DIP_4: R6.2, SW1.5, U2.22 (RB1)
/DRAIN: D1.2 (A), Q1.3 (D), U1.2 (COUT)
/ICSPCLK: J1.5, U2.27 (RB6/ICSPCLK)
/ICSPDAT: J1.4, U2.28 (RB7/ICSPDAT)
/MCLR: J1.1, R7.2, U2.1 (~MCLR)
/OSC1: C1.1, U2.9 (RA7/OSC1), Y1.2
/OSC2: C2.1, U2.10 (RA6/OSC2), Y1.1
/RELAY_24V: J4.1, U1.4 (SOUT)
/SCL: J2.2, J3.4, SCL.1, U2.14 (RC3)
/SDA: J2.1, J3.5, SDA.1, U2.15 (RC4)
/TRIG_PIN: R1.1, U2.13 (RC2)
GND: C1.2, C2.2, C3.2, C4.2, GND.1, J1.3, J2.3, J3.3, J4.4, J5.2, J6.1, J7.2, Q1.2 (S), R2.2, SW1.1, SW1.2, SW1.3, SW1.4, U2.8 (VSS), U2.19 (VSS), U3.2 (VSS), U3.8 (STBY)
unnamed: J2.5, J3.1

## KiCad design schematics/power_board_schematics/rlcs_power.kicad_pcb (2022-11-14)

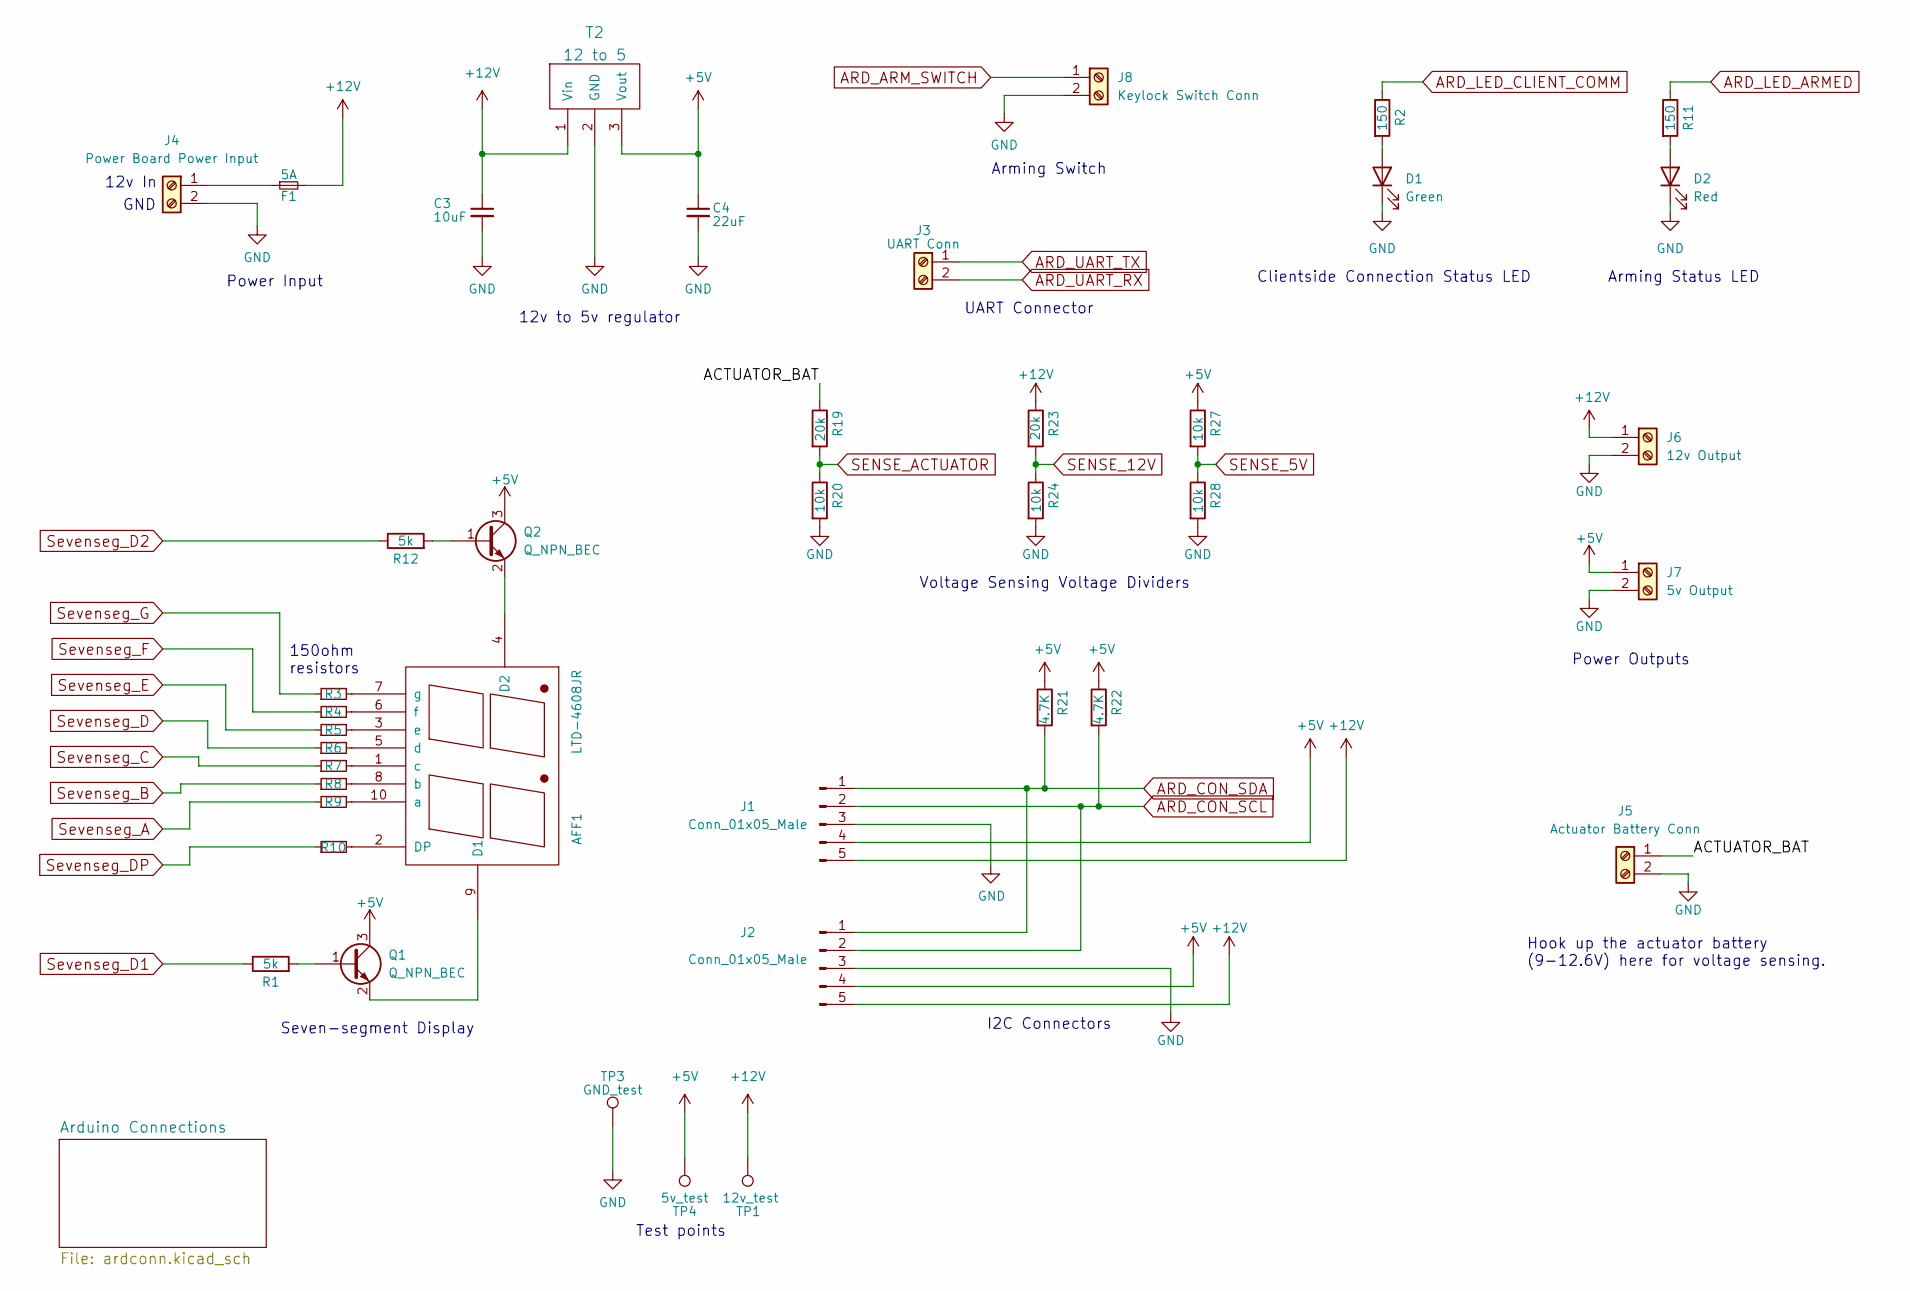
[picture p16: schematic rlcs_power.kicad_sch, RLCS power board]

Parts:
AFF1: LTD-4608JR
C3: 10uF; C_0805_2012Metric_Pad1.15x1.40mm_HandSolder
C4: 22uF; C_0805_2012Metric_Pad1.15x1.40mm_HandSolder
D1: Green; LED_1206_3216Metric_Pad1.42x1.75mm_HandSolder
D2: Red; LED_1206_3216Metric_Pad1.42x1.75mm_HandSolder
F1: 5A; Fuseholder5x20_horiz_open_inline_Type-I
J1, J2: Conn_01x05_Male; JST_EH_B5B-EH-A_1x05_P2.50mm_Vertical
J3: UART Conn; TerminalBlock_TE_282834-2_1x02_P2.54mm_Horizontal
J4: Power Board Power Input; TerminalBlock_Phoenix_MKDS-1,5-2-5.08_1x02_P5.08mm_Horizont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
J5: Actuator Battery Conn; TerminalBlock_Phoenix_MKDS-1,5-2-5.08_1x02_P5.08mm_Horizont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
J6: 12v Output; TerminalBlock_Phoenix_PT-1,5-2-5.0-H_1x02_P5.00mm_Horizontal
J7: 5v Output; TerminalBlock_Phoenix_PT-1,5-2-5.0-H_1x02_P5.00mm_Horizontal
J8: Keylock Switch Conn; TerminalBlock_TE_282834-2_1x02_P2.54mm_Horizontal
Q1, Q2: Q_NPN_BEC; SOT-523
R1, R12: 5k; R_0805_2012Metric_Pad1.20x1.40mm_HandSolder
R2, R3, R4, R5, R6, R7, R8, R9, R10, R11: 150; R_0805_2012Metric_Pad1.20x1.40mm_HandSolder
R19, R23: 20k; R_0805_2012Metric_Pad1.20x1.40mm_HandSolder
R20, R24, R27, R28: 10k; R_0805_2012Metric_Pad1.20x1.40mm_HandSolder
R21, R22: 4.7K; R_0805_2012Metric_Pad1.20x1.40mm_HandSolder
T2: 12 to 5; VXO78XX-1000
TP1: 12v_test; PinSocket_1x01_P2.00mm_Vertical
TP3: GND_test; PinSocket_1x01_P2.00mm_Vertical
TP4: 5v_test; PinSocket_1x01_P2.00mm_Vertical

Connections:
+5V: C4.1, J1.4, J2.4, J7.1, Q1.3 (C), Q2.3 (C), R21.1, R22.1, R27.1, T2.3 (Vout), TP4.1; also elsewhere on the board
+12V: C3.1, F1.2, J1.5, J2.5, J6.1, R23.1, T2.1 (Vin), TP1.1
/ACTUATOR_BAT: J5.1, R19.1
ARD_ARM_SWITCH: J8.1; also elsewhere on the board
ARD_CON_SCL: J1.2, J2.2, R22.2; also elsewhere on the board
ARD_CON_SDA: J1.1, J2.1, R21.2; also elsewhere on the board
ARD_LED_ARMED: R11.1; also elsewhere on the board
ARD_LED_CLIENT_COMM: R2.1; also elsewhere on the board
ARD_UART_RX: J3.2; also elsewhere on the board
ARD_UART_TX: J3.1; also elsewhere on the board
GND: C3.2, C4.2, D1.1 (K), D2.1 (K), J1.3, J2.3, J4.2, J5.2, J6.2, J7.2, J8.2, R20.2, R24.2, R28.2, T2.2 (GND), TP3.1; also elsewhere on the board
unnamed: AFF1.1 (c), R7.2
unnamed: AFF1.2 (DP), R10.2
unnamed: AFF1.3 (e), R5.2
unnamed: AFF1.4 (D2), Q2.2 (E)
unnamed: AFF1.5 (d), R6.2
unnamed: AFF1.6 (f), R4.2
unnamed: AFF1.7 (g), R3.2
unnamed: AFF1.8 (b), R8.2
unnamed: AFF1.9 (D1), Q1.2 (E)
unnamed: AFF1.10 (a), R9.2
unnamed: D1.2 (A), R2.2
unnamed: D2.2 (A), R11.2
unnamed: F1.1, J4.1
unnamed: Q1.1 (B), R1.2
unnamed: Q2.1 (B), R12.2
SENSE_5V: R27.2, R28.1; also elsewhere on the board
SENSE_12V: R23.2, R24.1; also elsewhere on the board
SENSE_ACTUATOR: R19.2, R20.1; also elsewhere on the board
Sevenseg_A: R9.1; also elsewhere on the board
Sevenseg_B: R8.1; also elsewhere on the board
Sevenseg_C: R7.1; also elsewhere on the board
Sevenseg_D: R6.1; also elsewhere on the board
Sevenseg_D1: R1.1; also elsewhere on the board
Sevenseg_D2: R12.1; also elsewhere on the board
Sevenseg_DP: R10.1; also elsewhere on the board
Sevenseg_E: R5.1; also elsewhere on the board
Sevenseg_F: R4.1; also elsewhere on the board
Sevenseg_G: R3.1; also elsewhere on the board

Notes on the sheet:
Hook up the actuator battery (9-12.6V) here for voltage sensing.
Arming Switch
UART Connector
12v In
GND
12v to 5v regulator
Clientside Connection Status LED
Voltage Sensing Voltage Dividers
Seven-segment Display
Power Input
Test points
I2C Connectors
Arming Status LED
150ohm resistors
Power Outputs

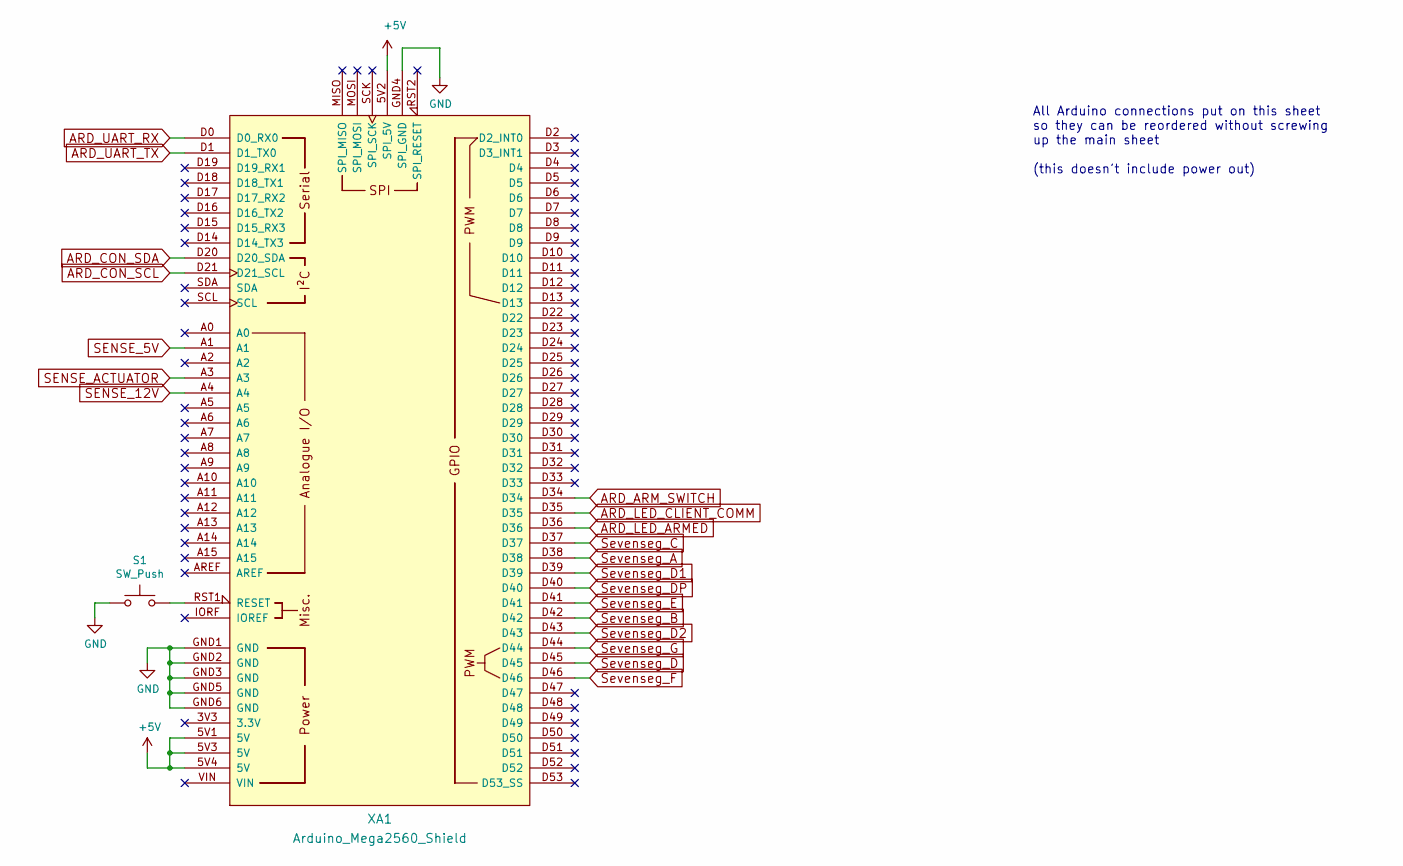
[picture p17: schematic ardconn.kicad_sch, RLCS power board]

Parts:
S1: SW_Push; SW_PUSH_6mm
XA1: Arduino_Mega2560_Shield

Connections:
+5V: XA1.5V1 (5V), XA1.5V2 (SPI_5V), XA1.5V3 (5V), XA1.5V4 (5V); also elsewhere on the board
ARD_ARM_SWITCH: XA1.D34; also elsewhere on the board
ARD_CON_SCL: XA1.D21 (D21_SCL); also elsewhere on the board
ARD_CON_SDA: XA1.D20 (D20_SDA); also elsewhere on the board
ARD_LED_ARMED: XA1.D36; also elsewhere on the board
ARD_LED_CLIENT_COMM: XA1.D35; also elsewhere on the board
ARD_UART_RX: XA1.D0 (D0_RX0); also elsewhere on the board
ARD_UART_TX: XA1.D1 (D1_TX0); also elsewhere on the board
GND: S1.1, XA1.GND1 (GND), XA1.GND2 (GND), XA1.GND3 (GND), XA1.GND4 (SPI_GND), XA1.GND5 (GND), XA1.GND6 (GND); also elsewhere on the board
unnamed: S1.2, XA1.RST1 (RESET)
SENSE_5V: XA1.A1; also elsewhere on the board
SENSE_12V: XA1.A4; also elsewhere on the board
SENSE_ACTUATOR: XA1.A3; also elsewhere on the board
Sevenseg_A: XA1.D38; also elsewhere on the board
Sevenseg_B: XA1.D42; also elsewhere on the board
Sevenseg_C: XA1.D37; also elsewhere on the board
Sevenseg_D: XA1.D45; also elsewhere on the board
Sevenseg_D1: XA1.D39; also elsewhere on the board
Sevenseg_D2: XA1.D43; also elsewhere on the board
Sevenseg_DP: XA1.D40; also elsewhere on the board
Sevenseg_E: XA1.D41; also elsewhere on the board
Sevenseg_F: XA1.D46; also elsewhere on the board
Sevenseg_G: XA1.D44; also elsewhere on the board

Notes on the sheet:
All Arduino connections put on this sheet so they can be reordered without screwing up the main sheet (this doesn't include power out)

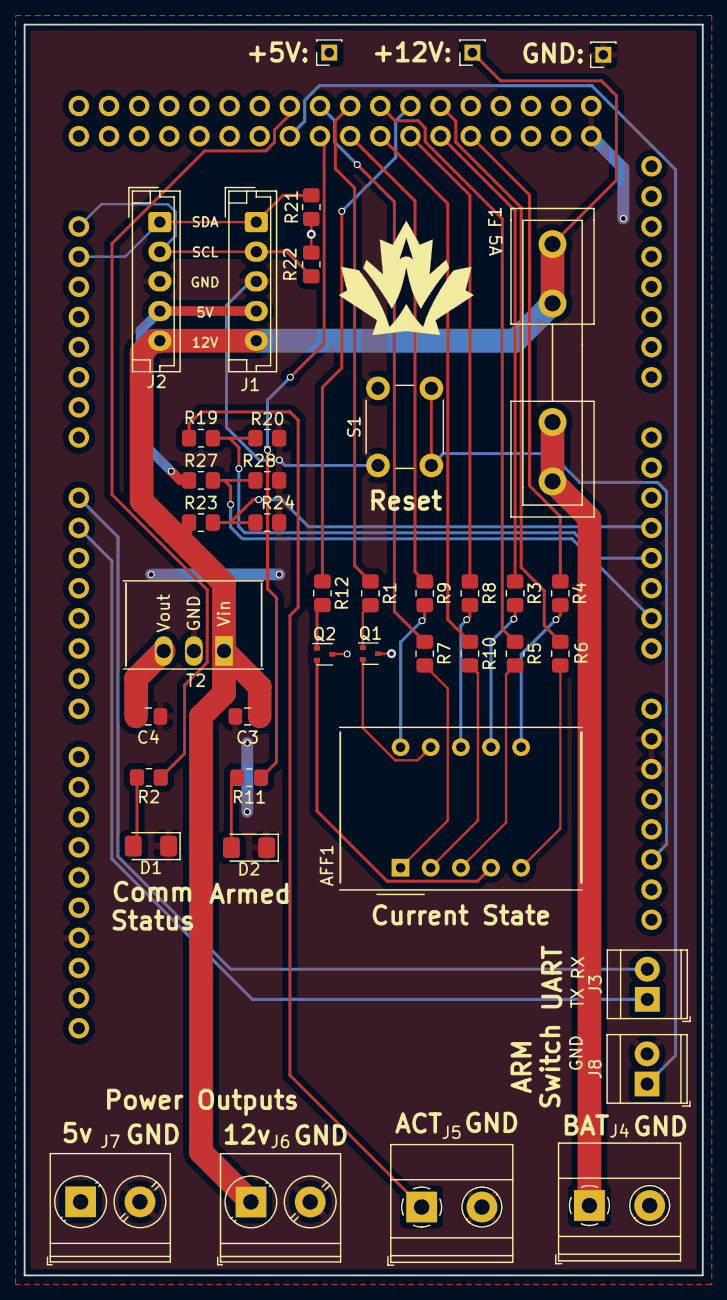
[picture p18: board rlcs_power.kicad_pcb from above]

Board: 2 copper layers, 57.1 x 105.4 mm, 42 parts (0 on the bottom side), 40 nets.

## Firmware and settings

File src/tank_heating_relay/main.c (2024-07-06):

#include <stdint.h>
#include <stdlib.h>
#include <xc.h>

#include "i2c.h"
#include "relay_general.h"
#include "timer.h"

#define MAX_LOOP_TIME_DIFF_CONST 500

uint16_t dip_inputs;

static void __interrupt() interrupt_handler(void) {
    // We received a i2c request from master, handle it.
    if (SSP1IF == 1) {
        i2c_handle_interrupt();
    }
    // Timer0 has overflowed - update millis() function
    // This happens approximately every 500us
    if (INTCONbits.TMR0IE == 1 && INTCONbits.TMR0IF == 1) {
        timer0_handle_interrupt();
        INTCONbits.TMR0IF = 0;
    }
}

void read_dip_inputs(void) {
    uint16_t new_dip = 0;
    // RB2 and RB3 used for voltage sensing
    new_dip |= (!PORTAbits.RA4) ? (1) : 0;
    new_dip |= (!PORTBbits.RB0) ? (1 << 1) : 0; // MSB
    new_dip |= (1 << 4);
    if (dip_inputs != new_dip) {
        dip_inputs = new_dip;
        i2c_slave_init(dip_inputs); // reinitialize i2c slave module with new slave address
    }
}

void setup(void) {
    OSCCONbits.IRCF = 0b1101; // Set internal oscillator clock speed to 4 mhz (default is 500k)

    TRISAbits.TRISA0 = 1; // 24V Sense
    TRISAbits.TRISA1 = 1; // Current Sense
    TRISAbits.TRISA2 = 0; // Power Control
    TRISAbits.TRISA3 = 1; // Thermistor
    TRISAbits.TRISA4 = 1; // DIP_1
    TRISBbits.TRISB0 = 1; // DIP_2
    TRISBbits.TRISB2 = 1; // Kelvin Sense
    TRISBbits.TRISB3 = 1; // Kelvin Sense
    TRISBbits.TRISB5 = 0; // LED

    ANSELA = 0; // DISABLE ANALOG INPUT ON PORT A, then enable port 0 and 1
    ANSELAbits.ANSA0 = 1; // 24V Sense
    ANSELAbits.ANSA1 = 1; // Current Sense
    ANSELAbits.ANSA3 = 1; // Thermistor

    ANSELB = 0; // DISABLE ANALOG INPUT ON PORT B
    ANSELBbits.ANSB2 = 1; // Kelvin Sense
    ANSELBbits.ANSB3 = 1; // Kelvin Sense

    // Configure FVR module
    // b[7] enables FVR
    // b[1:0] sets the reference to 4.096
    FVRCON = 0b10000011;

    // Configure ADC module
    // b[7] sets right justification, b[6:4] sets CS = FRC,
    // b[2]+b[1:0] sets Vss and FVR as references.
    ADCON1 = 0b11110011;
}

int main(int argc, char **argv) {
    setup(); // Set up digital + analog I/O
    timer0_init(); // Initialize timer
    set_power_off();
    set_led_off();
    dip_inputs = 0;
    i2c_slave_init(dip_inputs);
    read_dip_inputs(); // Get actual dip switch value to set slave address, init i2c

    uint32_t last_millis = millis();

    while (1) {
        // Heartbeat
        if (millis() - last_millis > MAX_LOOP_TIME_DIFF_CONST) {
            // One day I will configure this correctly, but ATM we only need the LED to blink ;-;
            last_millis = millis();

            led_heartbeat();
        }

        read_analog_inputs(CHANNEL_THERMISTOR);
        read_analog_inputs(CHANNEL_CURR_SENSE);
        read_analog_inputs(CHANNEL_24V_SENSE);
        read_analog_inputs(CHANNEL_KELVIN_N);
        read_analog_inputs(CHANNEL_KELVIN_P);

        read_dip_inputs(); // Check if dip switch input has changed, re-init i2c if so
    }
    return (EXIT_SUCCESS);
}

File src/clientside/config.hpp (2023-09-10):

#ifndef CONFIG_H
#define CONFIG_H

#include "common/config.hpp"
#include <stdint.h>

namespace config {

ActuatorMessage build_command_message();

constexpr unsigned long COMMAND_MESSAGE_INTERVAL_MS = 100;
constexpr unsigned long COMMUNICATION_RESET_MS = 50;
constexpr uint16_t COMMUNICATION_TIMEOUT_S = 3;

constexpr uint16_t BATT_SCALE_PRE_OFFSET = -11;
constexpr uint16_t BATT_SCALE_NUM = 1;
constexpr uint16_t BATT_SCALE_DEN = 7;

; // random semicolon to fix clangd warning bug, see: https://stackoverflow.com/questions/72456118/why-does-clang-give-a-warning-unterminated-pragma-pack-push-at-end-of-f
#pragma pack(push, 1)
struct USBMessage {
  ActuatorMessage actuator_msg;
  SensorMessage sensor_msg;
};
#pragma pack(pop)

} // namespace config

#endif

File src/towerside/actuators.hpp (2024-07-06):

#ifndef ACTUATORS_H
#define ACTUATORS_H

#include <stdint.h>

#include "common/mock_arduino.hpp"
#include "common/shared_types.hpp"
#include "errors.hpp"

namespace actuator {

class Actuator {
public:
  // The suggested actuator interface is
  // void set(bool value)
  // void get_<sensor>_<units>()
  // but it can be modified based on specific actuator requirements
};

class I2C: public Actuator {
  uint8_t slave_address; // slave address we are controlling
  virtual bool get_power(bool value __unused) {
    return true;
  }
  virtual bool get_select(bool value) {
    return !value; // Valves are wired up such that select being off means the valve is open
  }
public:
  I2C(uint8_t slave_address):
    slave_address{slave_address} {}

  void set(bool value) {
    Wire.beginTransmission(slave_address);
    // Relay boards have two relays. One turns on power, and the other selects which direction to apply power to.
    // LSB is power, next bit is select.
    bool power = get_power(value);
    bool select = get_select(value);
    bool healthy = true;
    healthy &= Wire.write((select << 1) | power) == 1; // returns the number of bytes written, should be 1
    healthy &= Wire.endTransmission() == 0; // returns non-zero value if there was an error
    healthy &= !Wire.getWireTimeoutFlag(); // make sure timeout flag is not set
    if (!healthy) {
      errors::push(slave_address, ErrorCode::I2CWriteError);
    }
    Wire.clearWireTimeoutFlag(); // if the flag was set, clear it for next time
  }

  ActuatorPosition::ActuatorPosition get_state() {
    // Cast to uint8_t to avoid warning about ambiguous overload
    uint8_t received = Wire.requestFrom(slave_address, static_cast<uint8_t>(1)); // returns number of bytes receieved
    if (received != 1) {
      errors::push(slave_address, ErrorCode::I2CReadError);
      return ActuatorPosition::error;
    }
    uint8_t lims = Wire.read(); // first byte returned is the limit switch values
    if (lims == 0) return ActuatorPosition::unknown;
    if (lims == 1) return ActuatorPosition::open;
    if (lims == 2) return ActuatorPosition::closed;
    return ActuatorPosition::error;
  }

  uint16_t get_current_ma(uint8_t channel) {
    if (channel > 1) { // Index must be 0 or 1 for primary or secondary
      return SENSOR_ERR_VAL;
    }
    // Cast to uint8_t to avoid warning about ambiguous overload
    uint8_t received = Wire.requestFrom(slave_address, static_cast<uint8_t>(5)); // returns number of bytes received
    if (received != 5) {
      errors::push(slave_address, ErrorCode::I2CReadError);
      return SENSOR_ERR_VAL;
    }
    Wire.read(); // limit switch values, ignore
    if (channel == 1) { // if we want the secondary current
      Wire.read(); Wire.read(); // ignore the first (primary) current value (2 bytes)
    }
    uint16_t adcl = Wire.read(); // get the 16-bit current reading
    uint16_t adch = Wire.read();
    return ((adch << 8) | adcl) * 4; // adc / 1024 (10bit) * 4096mV (vref) / 10mohm / 100 adc scaler * 1000 mV/V
  }
};

class Ignition: public I2C {
  virtual bool get_power(bool value) override {
    return value;
  }
  virtual bool get_select(bool value) override {
    return value;
  }
public:
  Ignition(uint8_t slave_address): I2C(slave_address) {}
};

class Heater {
  uint8_t slave_address; // slave address we are controlling
  bool power_set;

public:

  Heater(uint8_t slave_address):
      slave_address{slave_address},power_set{0} {}

  void set(bool value) {
    power_set = value;
    Wire.beginTransmission(slave_address);
    // LSB is power, bit [3:1] are for register select
    bool healthy = true;
    healthy &= Wire.write(power_set) == 1; // returns the number of bytes written, should be 1
    healthy &= Wire.endTransmission() == 0; // returns non-zero value if there was an error
    healthy &= !Wire.getWireTimeoutFlag(); // make sure timeout flag is not set
    if (!healthy) {
      errors::push(slave_address, ErrorCode::I2CWriteError);
    }
    Wire.clearWireTimeoutFlag(); // if the flag was set, clear it for next time
  }

  void select_reg(uint8_t reg){
    Wire.beginTransmission(slave_address);
    // LSB is power, bit [3:1] are for register select
    bool healthy = true;
    healthy &= Wire.write(power_set | (reg << 1)) == 1; // returns the number of bytes written, should be 1
    healthy &= Wire.endTransmission() == 0; // returns non-zero value if there was an error
    healthy &= !Wire.getWireTimeoutFlag(); // make sure timeout flag is not set
    if (!healthy) {
      errors::push(slave_address, ErrorCode::I2CWriteError);
    }
    Wire.clearWireTimeoutFlag(); // if the flag was set, clear it for next time
  }

  uint16_t get_thermistor() {
    select_reg(0);
    // Cast to uint8_t to avoid warning about ambiguous overload
    uint8_t received = Wire.requestFrom(slave_address, static_cast<uint8_t>(2)); // returns number of bytes received
    if (received != 2) {
      errors::push(slave_address, ErrorCode::I2CReadError);
      return SENSOR_ERR_VAL;
    }
    uint16_t adcl = Wire.read();
    uint16_t adch = Wire.read();
    return ((adch << 8) | adcl); // Return raw ADC values
  }

  uint16_t get_current_ma() {
    select_reg(1);
    // Cast to uint8_t to avoid warning about ambiguous overload
    uint8_t received = Wire.requestFrom(slave_address, static_cast<uint8_t>(2)); // returns number of bytes received
    if (received != 2) {
      errors::push(slave_address, ErrorCode::I2CReadError);
      return SENSOR_ERR_VAL;
    }
    uint16_t adcl = Wire.read();
    uint16_t adch = Wire.read();
    return ((adch << 8) | adcl) * 40; // adc / 1024 (10bit) * 4096mV (vref) / 1mohm / 100 adc scaler * 1000 mV/V
  }

  uint16_t get_batt_voltage() {
    select_reg(2);
    // Cast to uint8_t to avoid warning about ambiguous overload
    uint8_t received = Wire.requestFrom(slave_address, static_cast<uint8_t>(2)); // returns number of bytes received
    if (received != 2) {
      errors::push(slave_address, ErrorCode::I2CReadError);
      return SENSOR_ERR_VAL;
    }
    uint16_t adcl = Wire.read();
    uint16_t adch = Wire.read();
    return ((adch << 8) | adcl) * 28; // adc / 1024 (10bit) * 4096mV (vref) * 7.04
  }

  uint16_t get_kelvin_low_voltage() {
    select_reg(3);
    // Cast to uint8_t to avoid warning about ambiguous overload
    uint8_t received = Wire.requestFrom(slave_address, static_cast<uint8_t>(2)); // returns number of bytes received
    if (received != 2) {
      errors::push(slave_address, ErrorCode::I2CReadError);
      return SENSOR_ERR_VAL;
    }
    uint16_t adcl = Wire.read();
    uint16_t adch = Wire.read();
    return ((adch << 8) | adcl) * 28; // adc / 1024 (10bit) * 4096mV (vref) * 7.04
  }
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

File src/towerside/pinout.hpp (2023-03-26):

#ifndef PINOUT_H
#define PINOUT_H

#include <stdint.h>

namespace pinout {

const uint8_t MAIN_BATT_VOLTAGE = 4;
const uint8_t ACTUATOR_BATT_VOLTAGE = 3;
const uint8_t KEY_SWITCH_IN = 34;

const uint8_t SEVENSEG_D1 = 43;
const uint8_t SEVENSEG_D2 = 39;
const uint8_t SEVENSEG_A  = 38;
const uint8_t SEVENSEG_B  = 42;
const uint8_t SEVENSEG_C  = 37;
const uint8_t SEVENSEG_D  = 45;
const uint8_t SEVENSEG_E  = 41;
const uint8_t SEVENSEG_F  = 46;
const uint8_t SEVENSEG_G  = 40;
const uint8_t SEVENSEG_DP = 44;

const uint8_t COMM_STATUS_LED = 35;
const uint8_t ARM_STATUS_LED = 36;

} // namespace pinout

#endif

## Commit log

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2017-12-04 importing kicad projects to git
    More for centralization than for version control
    [Ignition.sch, Relay_assembly.sch, ardconn.sch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]
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2017-12-20 Getting the client side code to compile
    Most of the client side code was originally written in separate
    segments, without actually checking that it compiled. So a bunch of the
    function calls had the wrong names, or the linker freaked out because we
    weren't cross compiling to C++ correctly, a bunch of stuff like that.
    This commit fixes those "can't compile" issues.
    Note that this commit doesn't guarantee that the code _works_ at all,
    just that it now compiles properly. Still waiting on a test bed to
    ensure that it actually works (either a test script or another aruduino
    to test on).
    There's also some functionality that isn't in here, this only includes
    the core required FSM and button polli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
2018-01-09 Initial Commit, start drawing tower side backplane
    Added neccessary boards, that is 5 relay boards (one is redundant), one
    power board, and one arduino Mega. Need the dimensions of the box
    they'll be mounted in before continuing. I'll get those measurements
    tomorrow.
    [Tower_Side_Backplane.dwg]
2018-01-10 Add box dimensions and initial placements of boards
    Rough areas layed out based on first impressions of where they should
    go. Added another relay board for that sweet sweet redundancy.
    Next to do is measure battery holders and add them (and the associated
    holes) to the drawing, and start conceptually routing wires and adding
    routing cutouts and strain relief tie downs.
    [Tower_Side_Backplane.dwg]
2018-01-10 Add Client Side drawing done by Kylie
    Kylie drew a client side panel last term, adding it to git tracking
    [Client_Side_Panel.dwg]
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2018-01-10 Add proper dimensions to keyswitch, contrast pot, and ignition button
    Using the following digikey part numbers
    keyswitch - EG2625-ND
    contrast pot - 987-1659-ND
    ignition pushbutton - EG4699-ND
    [Client_Side_Panel.dwg]
2018-01-11 Add 3 battery holders to tower side backplane
    Assuming that we're running the same batteries (they're cheap as hell
    and worked awesome in IREC 2017). The system could easily be run off of
    a single battery (they hold a lot of charge), but by having multiple we
    can run the actuators off of a separate power supply than the arduino
    and xbee. Three should be more than overkill, one holder might not even
    need to be populated.
    [Tower_Side_Backplane.dwg]
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2018-01-12 Change Power board Arduino connector
    Also, the 15v power regulator no longer shorts its NC pins to ground
    (this isn't changed in this commit, it was changed before these
    schematics were added to github).
    [ardconn.sch, rlcs_power.kicad_pcb]
2018-01-12 Replace bidirectional shifter for SD card
    Now MOSI and SCL run through voltage dividers, and MISO is just a wire.
    [ardconn.sch, rlcs_power.kicad_pcb, rlcs_power.sch]
2018-01-14 Change SevSeg digital writes HIGH/LOW
    Testing was done on a common cathode 7seg, the real board has a common
    anode. So all the outputs needed to be flipped.
2018-01-14 Add Arduino and power supply board to client side drawing
    No idea where to put the batteries, mostly hoping the box is deep enough
    that it doesn't matter. Need to start setting aside space to run wire, but
    that should be a nonissue.
    [Client_Side_Panel.dwg]
2018-01-17 Actually make it a 2.54mm pitch connector
    whoops, I had a 2mm pitch one, now it's fixed and is proper. DRC passes
    with flying colours.
    [ardconn.sch, rlcs_power.kicad_pcb]
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2018-01-17 Change fusing from bottom side to top side
    Correct that error. Also add flyback diode to relay board
    [Relay_assembly.sch, rlcs_power.kicad_pcb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]
2018-01-19 Add wires and zip tie cutouts to client side drawing
    Still preliminary, will need review.
    [Client_Side_Panel.dwg]
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2018-01-19 Add test cut to check sizes and footprints
    Needed a smaller thing I could cut to ensure that the footprints were
    all the right size, the holes were proper size, the grommets fit, and
    the zip tie thing held wires.
    After making this test cut on 2018-01-19, can confirm that the arduino
    mega footprint, the power board footprint, the battery holder footprint
    is correct, and the zip tie cutouts work a treat. Issue, however, is
    that the holes (1.5mm radius) are too big (actually, they make
    excellent clearance holes, but terrible tapped holes), so for all tapped
    holes we should take them down to 1.25mm radius.
    Test cut looks good, proceeding with real cut so that I can assemble the
    box and bring i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
    [Tower_Side_Backplane.dwg]
2018-01-19 Ready for first version of full print
    Changed hole dimensions to 2.5mm diameter, removed test print section,
    added fillet to outside of cutout to remove the pointy bits.
    [Tower_Side_Backplane.dwg]
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2018-01-23 Silkscreen fix on power board
    Battery terminal label wasn't where it should have been. It now is
    [rlcs_power.kicad_pcb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]
2018-01-23 Rename Relay board gerbers to match elecrow expected format
    [rlcs_relay.GBL, rlcs_relay.GBS, rlcs_relay.GTL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]
2018-01-25 Change gerber top mask to be correct
    There was an error in which I had a silkscreen file in .gts instead of a
    soldermask gerber. Error has been corrected.
    [rlcs_power.GTS]
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2018-01-30 Add label rasters to client side, add test cut
    Ready to print on Thursday, assuming approval from Miranda
    [Client_Side_Panel.dwg]
2018-02-02 Move things around because the LCD takes up space _beyond_ it's cutout
    [Client_Side_Panel.dwg]
2018-02-02 Add a title to the Client side cutout
    [Client_Side_Panel.dwg]
2018-02-02 Changes based on test print. Last commit before full print
    [Client_Side_Panel.dwg]
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2018-02-15 Makefile fixes
    Recompile all source files whenever any of our header files change, this
    should avoid bugs like "hey, how come it's still polling pin 12 when I
    told it to poll pin 30".
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2018-03-31 Clean up SevSeg code to reduce memory usage
    Switch some strings into uint8_ts, remove some loops, get rid of master
    object (i have some major issues with the concept of OOP)
2018-04-01 Create SD handling code
    Doesn't currently log anything, and isn't integrated into tower side yet
    (only client side), but it's a start. should this be put on its own
    branch and not put in development code into master? Probably.
    Basic support for buffered output and message timestamps - could likely
    be improved. Buffer size of 1K was chosen completely arbitrarily -
    subject to change.
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2018-04-03 Turn on SevSeg display on tower power board
    Currently outputs its own state. Strangely, it doesn't match button
    state on the client board. Don't know why. Will figure that out later
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2018-04-07 Misc fixes
    remove TODOs that had been finished from LCD.cpp and from
    client_pin_defines.h, added another check to
    tower_globals.c::apply_state to register a change in one of the actuator
    states that wasn't tracked, and fixed the SevSeg output (it was
    displaying the ascii value of a base64 number, not the hex
    representation of the value)
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2018-04-17 Add unit test to nodeio.ioio
    It's a random unit test that generates 10000 random sensor_data_t's,
    pushes them all through "pack_sensor_data", pulls them through
    "unpack_sensor_data", and checks that they're equal. Basic test, but it
    doesn't currently pass, because the "unpack_sensor_data" function hasn't
    been written. That's up next.
2018-04-18 Create drawings for the xbee holder box
    There are no mounting holes. That's considered an excercise for the
    drill. Used FreeCAD because I don't have a windows box. These boxes are
    already printed (Thanks Veronica!), and they mostly work I think
    [bottom_half.stl, top_half.stl, xbee mount.FCStd]
2018-04-19 Finish unpack sensor data, unit test now passes
    The sensor decoding is kinda wonky (by design). It only allows 9 bits of
    precision from the pressure reading (bits 9:1 of that parameter) and 6
    bits of precision from the thermistor readings (bits 9:3). Make sure to
    scale your values appropriately. This is fixeable, it's just that way to
    reduce number of bytes that have to go over the radio link. If we decide
    that the full 10 bits of ADC precision are absolutely necessary, that
    can be added in.
2018-04-19 Write sensor data send function
    this code should now be fully functional (it has not been integration
    tested even a little bit, so take with grain of salt). API is now fixed,
    I promise not to fuck with it from here on out.
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2018-05-19 Change tower to use Serial1 for XBEE
    I got tired of being unable to reprogram the arduino while the xbee was
    plugged in, so I moved it to another Serial interface. This also fixes
    the issue where on startup, the tower arduino would see bytes available
    on its serial lines, and think it was being reprogrammed, and not leave
    the bootloader. So that's nice
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2018-05-20 Add rocket valve state to the output of the LCD
    Currently nodeio.ioio doesn't update the daq holder, so the outputting
    doesn't _do_ anything, but at least now it's there
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2018-05-23 small LCD fix
    It was drawing the currents for ignition in the wrong place, it is no
    longer doing that
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2018-05-25 Remove Actuator current reading
    We never used it for anything, so we can totally get rid of it.
    I didn't remove ignition current reading. That would be dumb.
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2018-05-27 Fix nodeio.ioio sensor values handling bug
    Also adds debug logs that were used to identify the bug
2018-05-27 Change arduino_programs directory name to src
    It bugged the hell out of me that it was a non-standard filenaming
    convention
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2018-06-10 Split ignition onto two boards
    It's now both more safer and more redundant. Two relays/mosfets need to
    fail before we accidentally set off of the rocket. Also, if we blow a
    fuse when firing primary, we don't also screw up secondary.
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2018-06-16 Add nodeio.ioio update tests
    They're currently broken, because I can't write a logging system right,
    but knowing your faults is the first step towards fixing them
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2019-05-10 Replace lsw values in daq_t to valve_states
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2019-05-28 Fix bug that opened injector valve on RLCS startup
    The tower side box's desired rocketCAN state wasn't being initialized,
    so everything was set to 0. That caused both valves to default to OPEN,
    which is great for vent, but suboptimal for injector.
    This commit forces injector to NOTHING on RLCS startup, which causes the
    valve to be depowered, which is all of what you want, and none of what
    you don't.
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2019-05-31 Fix DAQ readings on the pressure sensors
    There was an issue with the sensor SP1 in which it would not report any
    pressures below 500psi (reporting all of them as 500psi). Debugging this
    issue, it was found to be that one of the pins on the arduino (pin A6)
    had failed in some way, and was providing a voltage of 2.5V (likely from
    a diode to VDD). This problem was fixed by changing the SP1 pin to A4.
    This commit also adjusts the pressure sensor calibration constants, as
    found on a somewhat sketchy 5 point manual pressure guage calibration.
    Should be good for WDR, we may want to recalibrate for IREC.
2019-06-05 Add ability to transfer battery voltages over radio
    Tower can now send the battery voltages of tower actuators battery,
    tower main battery, rocket vent battery, and rocket bus battery to the
    client box. It doesn't _read_ these voltages yet, but some day it will.
    And when it does, by god we'll be ready.
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2020-02-24 Fix current sensing and client side battery sensing.
2020-02-26 Fix valve safe states.
2020-03-04 Add changes for RLCSV3 tower side Overhaul (#15)
    Add Schematics and PCB layout for new relay boards for rlcsv3
    [Ignition.sch, Relay_assembly-2019-10-27-12-36-42.sch, Relay_assembly-2019-10-27-12-39-45.sch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]
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2020-03-09 Add functionality for Wire library
    Replaced linac.c, tower_daq.c, tower_fsm.c and tower_globals.c with respective cpp files
2020-03-09 Fixed RA7 issue and added i2c functions.
    [main.c]
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2020-03-09 Add changes to fix Alex's comments
    Modify .gitignore to untrack unwated files.
    [main.c]
2020-03-09 Fix clock speed bug
    Add LED test code for initial testing
    [main.c]
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2020-03-14 Fix bug with dipswitch
    [main.c]
2020-03-15 Clean up codebase
    Fix indentation.
    Fix warnings generated byt compiler.
    Make code more "user friendly".
    [i2c.c, main.c, relay_general.c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]
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2020-05-28 Set CD and WP to 54 and 55 respectively
    [TREQ1O'[file5EB6340D.sch, ardconn.sch, rlcs_power-2020-05-25-11-18-40.sch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]
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2020-06-14 Fixed the reference designators
    [ardconn.sch, rlcs_power.sch]
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2020-11-29 Revert "More tweaks from review"
    This reverts commit 4e0c8d71b3290d9faf8db479f6ec01670aabe4c2.
    [i2c.c, main.c, relay_general.c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]
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2021-01-11 Add current rating to relay board fuse (#24)
    [rlcsv3_modular.sch]
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2021-01-21 Fix 7 segement display pins to make routing easier and fix footprints
    [ardconn.sch, rlcs_power.kicad_pcb, rlcs_power.sch]
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2021-02-09 Address second round of review and export gerbers
    [rlcs_power-B_Cu.gbr, rlcs_power-B_Mask.gbr, rlcs_power-B_SilkS.gbr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]
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2021-02-14 fix a couple silk screens
    [rlcs_power.kicad_pcb]
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2021-02-14 fix silk screens that broke from chaning footprints
    [ardconn.sch, rlcs_power.kicad_pcb]
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2022-02-07 Add voltage sensing, fix transistor footprint and redo shield (#30)
    * Add voltage sensing, fix transistor footprint and redo shield
    * Added resistors to transistors, generate pdf and gerbers
    * Review fixes
    * Make 12V traces support higher current, review fixes
    [ardconn.kicad_sch, ardconn.sch, high_side_switch_bjt.sch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]
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2022-10-08 Add Client Connection and Arm status indicator LED to Towerside Power Board schematic
    [ardconn.kicad_sch, rlcs_power.kicad_sch]
2022-10-08 Fix resistor label typo in Towerside Power Board schematic
    [rlcs_power.kicad_sch]
2022-10-08 Add UART connector to Towerside Power Board schematic
    [ardconn.kicad_sch, rlcs_power.kicad_sch]
2022-10-08 Move 12v sensing from analog input A0 to A4 on Towerside Power Board
    [ardconn.kicad_sch]
2022-10-09 Replace battery connector with screw terminal on Towerside Power Board
    [rlcs_power.kicad_sch]
2022-10-09 Swap Sevenseg D1 and D2 label on Towerside Power Board schematics
    [ardconn.kicad_sch, rlcs_power.kicad_sch]
2022-10-09 Replace J6,J7 connector with screw terminal on Towerside Power Board
    [rlcs_power.kicad_sch]
2022-10-10 Remove 3.3V circuit from Towerside Power Board
    Remove 3.3V regulator
    Remove 3.3V sensing
    [ardconn.kicad_sch, rlcs_power.kicad_sch]
2022-10-10 Replace actuator battery connector with a screw terminal on Towerside Power Board
    Replace J4 battery connection with a larger screw terminal
    Use large screw terminal for J5 actuator battery connection
    [rlcs_power.kicad_sch]
2022-10-10 Add arming switch connector to Towerside Power Board
    [ardconn.kicad_sch, rlcs_power.kicad_sch]
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2022-10-10 Add power switch connector to Towerside Power Board
    [rlcs_power.kicad_sch]
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2022-10-11 Only use 12v power input for Towerside Power Board
    [rlcs_power.kicad_sch]
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2022-10-22 Update Power Board schematic based on Confluence documention
    [ardconn.kicad_sch, rlcs_power.kicad_sch]
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2022-10-23 Fixed CAN transceiver
    [Hardwired CAN support.kicad_sch]
2022-10-23 Fix test points layout on Towerside Power Board schematic
    [ardconn.kicad_sch, rlcs_power.kicad_sch]
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2022-10-31 Fix footprints on Towerside Power Board
    [rlcs_power.kicad_sch]
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2022-11-04 WDR code changes (#36)
    * WIP WDR firmware
    * Fix relay I2C order
    * Remove default states, fixes for WDR
    * Show towerside status LEDs on client side, apply safe states even when disarmed
    * update current sense resistor value
    * Add checksum support
    * invert valve polarity
    * Set up two ignition boards for comp
    [actuators.hpp, clientside.ino, config.cpp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]
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2022-11-08 Towerside Power Board Routing fix
    [rlcs_power.kicad_pcb]
2022-11-25 clean up on wire spacing, power errors, add diode to actuator
    [Ignition.sch, Relay_assembly-2019-10-27-12-36-42.sch, Relay_assembly-2019-10-27-12-39-45.sch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]
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2022-11-28 reverse pinout on P2 connector
    [relay_board.kicad_sch]
2022-12-03 Clean up on relay board symbol library name and symbol names and add protection diodes to G1/G2 terminals on actuator header
    [relay_board.kicad_sch]
2023-01-05 Filled in missing R16 value, updated D5 symbol, added optional diodes D6/D7
    [relay_board.kicad_sch]
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2023-01-07 fixed reversed 12V power connectors and cleaned up silkscreens
    [relay_board.kicad_pcb]
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2023-01-12 Reversed the 5-pin and 2-pin screw terminals to match CAN support board
    [relay_board.kicad_pcb, relay_board.kicad_sch]
2023-01-19 added missing decoupling cap to PIC VDD, moved decoupling caps closer to ICs, fixed main power connections, small tweaks to trace routing
    [relay_board.kicad_pcb, relay_board.kicad_sch]
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2023-04-29 Fix injector valve safe state
    [config.cpp]
2023-05-18 Update CAN support code to act as +24V relay (#44)
    * Update CAN support code to act as +24V relay
    * Invert RLCS power state
    * WDR code changes
    [config.cpp, config.hpp, i2c.c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]
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2023-09-10 Client-side board (#41)
    * Add initial clientside board schematic
    * Complete client-side board schematic
    * Assign footprints to RLCS Client-side board
    * Fix schematic issue on Client-side board
    * Split missile switch to a new sheet for Client-side board
    * Update client-side board schematic
    * Update Client-side board schematic for reduce routing complexity
    * Add client-side board layout
    * Create NHD-0420DZ-FSW-FBW KiCAD footprint
    * Update Client-side board layout
    * Update clientside board layout
    * Add clientside board routing
    * Add clientside board silkscreen
    * Add name to client-side board silkscreen
    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
    [arduino_conn.kicad_sch, clientside_board_schematics.kicad_pcb, clientside_board_schematics.kicad_sch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]
2023-10-05 Repository Cleanup (#47)
    * Remove old files
    * Remove unused submodules
    * Update README
    * README terminology update
    * Remove mechanical drawings
    [Client_Side_Panel.dwg, Tower_Side_Backplane.dwg, bottom_half.stl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]
2023-12-13 LSF2 safe states (#48)
    * Update RLCS Clientside new pinout in code
    * Update LSF2 proposed safe state
    Update clientside ignition current display format
    * Fix ignition current sensing with new relay boards
    * Change VA2 safe state to open for LSF2
    [actuators.hpp, config.cpp, config.hpp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]
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2024-06-12 Tank heating control board (#52)
    * Add tank heating control board schematics
    * Add Tank Heating Control Board schematics PDF
    * Add thermistor and voltage sensing to schematics
    * routed
    * Change current sense to low side
    * Specify JLC part number location
    * Fix silkscreen
    * Fix ground and add gerber
    [relay_board-B_Cu.gbl, relay_board-B_Mask.gbs, relay_board-B_Paste.gbp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]
2024-07-06 Tank heating + WDR Firmware Edit (#53)
    * Add tank heating relay board firmware
    * Add ADC sensing to tank heating relay board code
    * WDR RLCS firmware except tank heating control
    * Update tank heating PIC code for ADC workaround
    * WDR + Tank Heating edits
    * Address comments, have not been tested
    [actuators.hpp, config.cpp, config.hpp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]
2024-07-07 2024 WDR1 Firmware Fix (#54)
    * Comment out disconnected secondary ignition
    * Add missing files in tank heating relay board firmware
    [config.cpp]
2024-07-13 2024 wdr3 fix (#55)
    * Swap fill-dump and vent valve switch location
    * Bring back second ignition relay board
    * Add tank heating status display on clientside
    [config.cpp, config.hpp]
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2025-07-17 Fixed solenoid states (#62)
    * Fixed solenoid states
    * LSF5
    * LSF5 for real
    * Fixed compilation errors
    * Fixed the OV103 States
    [config.cpp, config.hpp, seven_seg.cpp]
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
